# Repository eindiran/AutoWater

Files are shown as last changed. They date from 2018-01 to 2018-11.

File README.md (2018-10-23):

# AutoWater
AutoWater is a project which automates watering a potted plant by measure soil moisture levels using a capciative moisture sensor. If the water levels are beneath a threshold, AutoWater will trigger a normally-closed solenoid valve, pumping water into the pot.

## Ingredients
In order to begin this project you will need:
- __Arduino Uno__ or compatible board, with a __9v power supply__ (1)
- __TIP 120 transistor__ (1)
- __1N4007 Diode__ (1)
- __1k Ohm Resistor__ (1)
- [__Analog Capacitive Soil Moisture Sensor v1.0__](https://www.dfrobot.com/wiki/index.php/Capacitive_Soil_Moisture_Sensor_SKU:SEN0193) (1)
- __Breadboard__ (1)
- __Jumper wires__ (10+)
- __Alligator clamps__ (2)
- __Solenoid Valve__ (1)
- __Plastic tubing__ (10 feet)
- __Potted plant__ (1)

## Reading the moisture sensor
The first step is to set up the moisture sensor and get a reading off of it.
In the tests directory, there is a file which can be used to run the test: `MoistureSensorTest.ino`

Place the moisture sensor carefully in the potted plant, leaving the wire section exposed. Notice that on the sensor there is a horizontal white line: *do not submerge the sensor beyond this line*, as it is possible to damage the sensor if the top gets wet. Ideally place the sensor such that the dirt level is approximately __1 inch__ below this.

Take three jumper wires (1 red, 1 black, 1 blue). Match them to the same colors coming off of the sensor. Run the red wire into the __5v__ pin on the Arduino: this will provide power to the sensor. Next run the blue wire to the __Analog 0__ pin, and the black wire to the ground pin (__GND__).

### Moisture Sensor diagram
Here is a diagram showing the connections between the Arduino and the moisture sensor:

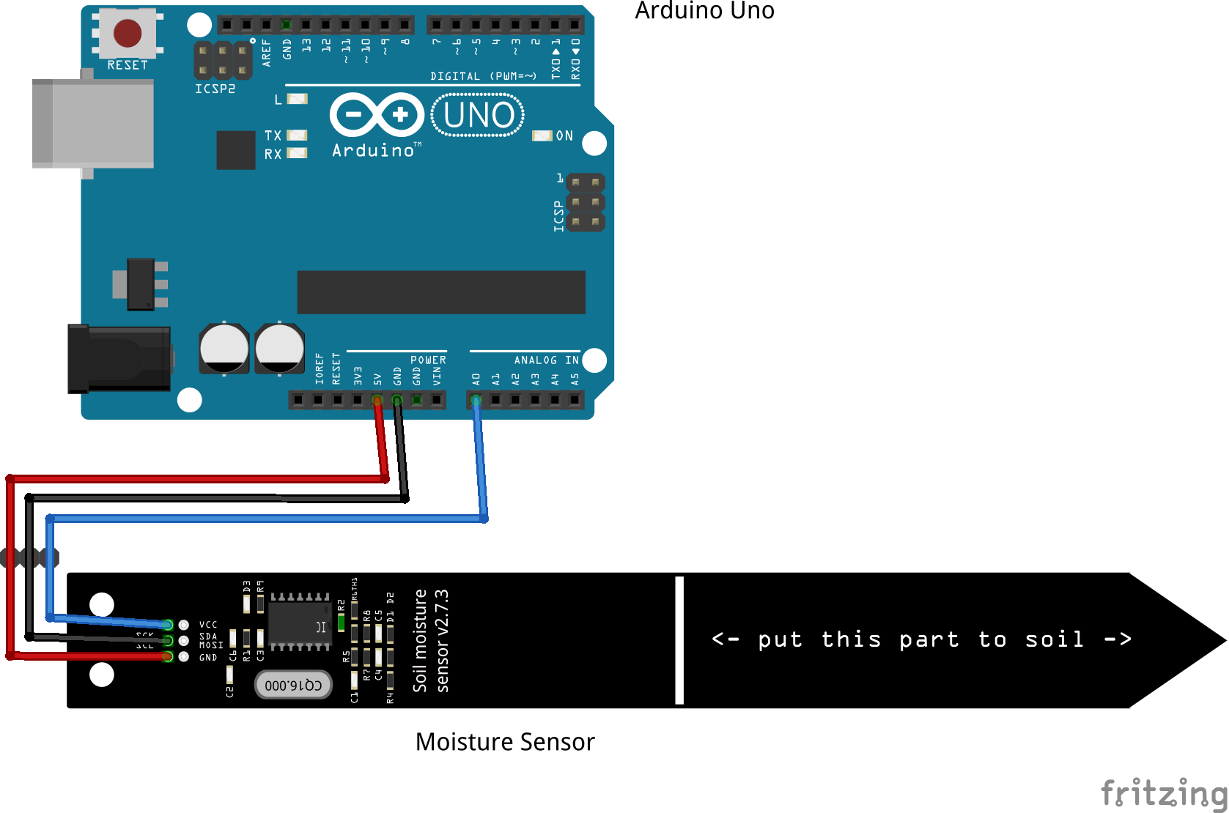
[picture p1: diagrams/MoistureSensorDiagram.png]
Moisture Sensor Diagram


### Testing the moisture sensor
Plug in the Arduino to your computer, then open the __Arduino IDE__ and upload `MoistureSensorTest.ino` to it. If you get permissions issues and can't upload it, look up the error message it spits out. Likely you will need to run a command like `sudo chmod a+rw /dev/ttyACM0`, which will give you write permissions for the Arduino.

Once you have successfully uploaded the file to the board, from the __Tools__ menu of the IDE, select __Serial Monitor__. If everything has been set up correctly, the window which opens will display a reading from the sensor which is updated every few seconds.
If the monitor displays nonsensical symbols instead of human-readable text, make sure that the baud rate for the monitor matches what is set in the code: using the vanilla code, set to __9600 Bd__.

In order to be sure that the sensor is working proper, after you have begun to see readings from it, slowly add water to the plant. Pour carefully, taking care to not splash the sensor directly. Gradually the reading from the sensor should *decrease* in value.

### Calibrate moisture sensor (optional)
This step is optional, depending on the accuracy you want the moisture sensor to report human-readable moistures with (e.g. "75% Humidity").

To calibrate your moisture sensor, follow the steps above to set it up for testing. In addition you will need a glass of water. First, dry off the moisture sensor entirely. Then fire up `MoistureSensorTest.ino`, and record the value that the sensor reports while held outside of any soil, in the air. Write down this value, which will be used as the 0% Humidity value.

Next, submerge the sensor up to the horizontal line in the glass of water. After the readings stabilize, write down the number, as this will be used as the 100% Humidity value.

Once we've captured these two values, open up the Arduino IDE, as we are going to make some small changes to the code. First find a global variable named `DEBUG`. It is set to __0__. Change the value to __1__. Next, find the variables `AIR_VALUE` and `WATER_VALUE`.
Change the value for the first from __1000__ to the number you recorded when calibrating the moisture sensor in the air.
Next, change the value for the second from __200__ to the value you recorded when calibrating the moisture sensor in the cup of water.
Finally, we need to make the interval correct. Find the variable `INTERVAL`. You need to set this value to `(AIR_VALUE - WATER_VALUE)/4`. Originally the variable was set like so: (1000 - 200)/4 = 800/4 = 200. If the result gives you a fraction, round to the nearest integer.

Save the code and re-upload it to the Arduino. Re-run the test in the air, water and soil, and see what values you get. Now you should see lines like "*Humidity: >50%*" in the output, which indicates that the humidity is >50 % and <75 % of `WATER_VALUE`.

## Turning the Solenoid Valve
Here is a diagram showing the setup of the solenoid valve.
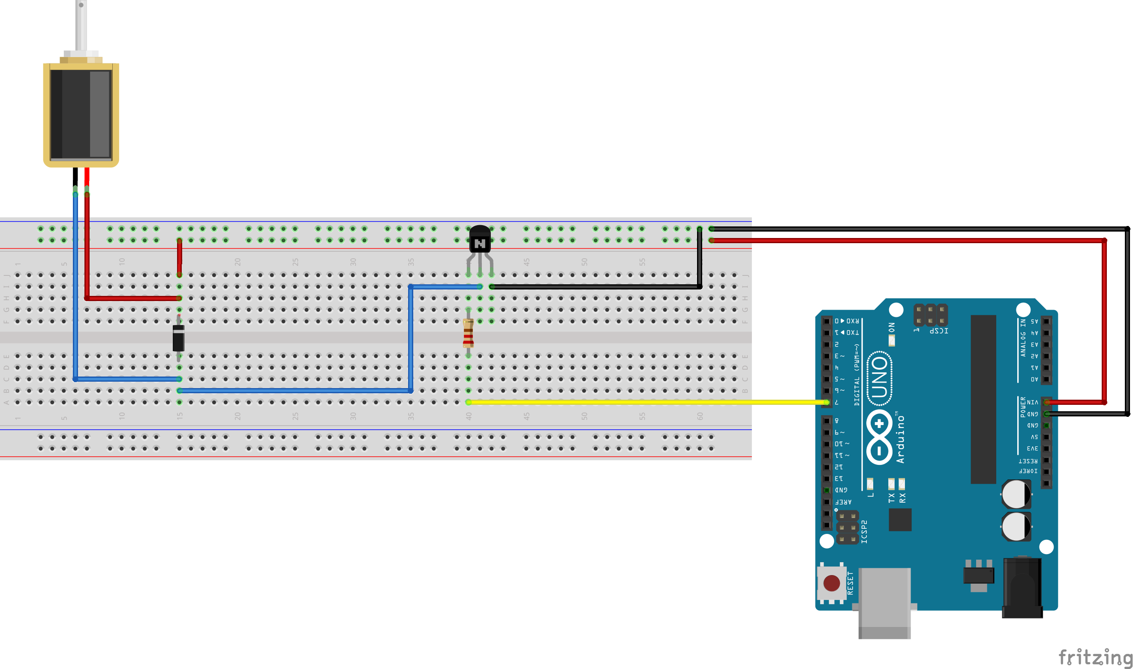
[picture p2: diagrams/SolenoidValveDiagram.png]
Solenoid Valve setup


The setup in this section is based on a tutorial from BC Robotics, which can be found [here](https://www.bc-robotics.com/tutorials/controlling-a-solenoid-valve-with-arduino/).

Note that none of the pins used here overlap with those used during the moisture sensor test. As a result, you don't need to unplug anything from the previous step. If you leave the moisture sensor plugged in during the next step, all the pieces will be correctly set up.
If you want to just play around with the solenoid valve setup, however, feel free to start with a clean breadboard.

### Setting up the power to the solenoid valve
To begin with turn the breadboard so that __j1__ is in the top left corner. Next, take a red wire and connect it to the __Vin__ pin on the Arduino. Plug this in to the __positive rail__ on the top right of the breadboard. This will take the direct voltage from the __9v__ power supply and pass it to the solenoid valve, without first sending it to the board's regulator. If you tried to use a lower voltage, the solenoid valve would not be able to turn. With another red wire connect the positive rail to the near end of a column, on the left side of the breadboard. Immediately below plug in another red wire; take an __alligator clamp__ and attach it to this wire. Connect the other end of this alligator clamp to the __positive__ side of the __solenoid valve__.

### Setting up the Diode
Take the __diode__ and put the side with the __white line__ immediately beneath the last wire plugged in to the breadboard. Plug the other end into __row c__ of the same column. In __row b__ plug in a black wire. Take the second alligator clamp and attach it first to this black wire, then to the __negative__ side of the solenoid valve.

### Setting up the Transistor
Take the __TIP-120 transistor__ and find the front. With the transistor facing you, plug all three pins into three columns in __row j__ beginning several columns to the right of the diode column. Take a black wire and plug it first into __row a__ of the diode column, then into __row i__ of the column containing the transistor's __middle pin__. Take the __resistor__ and plug it into the column of the __left pin__, leaving at least one open pin; in __row a__ of the same column, plug in a yellow wire. Plug the other end of the yellow wire into __digital pin 7__ on the Arduino.

### Setting up the ground
In the column of the __right pin__ of the transistor, add a black wire. Run this wire into the __ground rail__ at the top of the breadboard. Take another black wire and run it from one of two __GND__ pins on the Arduino to the ground rail on the breadboard. The circuit is now complete!

### Running the tests
Open up the IDE and connect the Arduino to your computer. Upload the file `SolenoidTest.ino`. Pick up the solenoid valve and put it next to your ear. You should hear it turn once per second.

Unplug the Arduino. Take a short length of __aquarium tubing__ and cut it off, placing one end inside the solenoid valve and the other end inside the __water reservoir__ or __pump__. Cut off a second length of tubing and put it into the other side of the solenoid valve. For the test, place this other end inside a bucket.

Plug the Arduino back in and run `SolenoidTest.ino` again. The valve should alternate between opening for a second and closing for a second, letting water out into the bucket each time it is open.

## Putting it all together
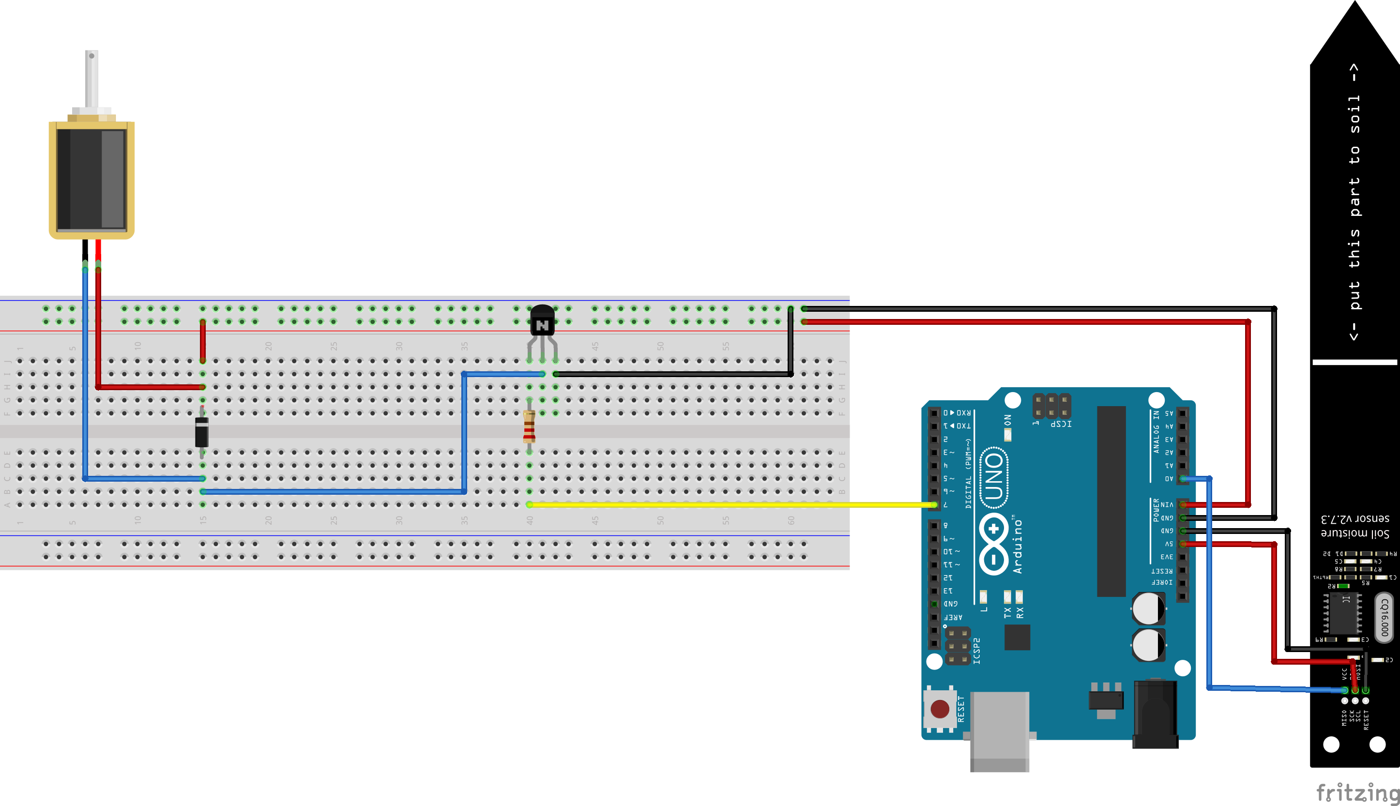
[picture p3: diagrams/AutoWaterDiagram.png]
AutoWater diagram

If you didn't unplug the moisture sensor during the last step, congratulations! You are almost ready to run AutoWater. If you did, follow the instructions for plugging in the moisture sensor while leaving all the wires from setting up the solenoid valve plugged in.

The last step before you run everything is connecting the potted plant. First place the moisture sensor in the soil, then take the output side of the tubing amd place it so that the output water will end up watering the plant, but not directly on the moisture sensor.

Open up `AutoWater.ino` in the IDE and edit the file to fit the values calibrated during the moisture sensor testing phase. Set the `DEBUG` value to the appropriate level of logging: __0__ has minimal logging, __1__ has normal logging, and __2__ has logging set to max while disabling the actual watering functionality. This last mode is very useful for debugging and experimenting.

Upload the completed file to the Arduino and open the __Serial Monitor__. Immediately you should see a reading from the moisture sensor. If that reading is too low and `DEBUG < 2`, AutoWater will water your plant! Once you've played around for a bit and have a good idea of how things work, change the time variables to fit the watering needs of your plant. Now you can happily go about your day knowing that the needs of your plant are being taken care of!

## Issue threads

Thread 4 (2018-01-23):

Fix Moisture Sensor Diagram

eindiran, 2018-01-23:
Fix Moisture Sensor Diagram to have red wire point into 5v on Arduino Uno.

eindiran, 2018-01-28:
Fixed a while back but forgot to close the issue.

Closed 2018-01-28.

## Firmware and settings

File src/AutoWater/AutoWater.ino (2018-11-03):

/**
 * AutoWater.ino
 * Automate watering a plant using a solenoid valve
 * and a moisture sensor.
 * Author: eindiran <eindiran@uchicago.edu>
 */

/** Initialize globals */
const int DELAY_SECONDS = 5;   // Time between moisture checks
const int AIR_VALUE = 1000;    // Replace this value with sensor reading of air
const int WATER_VALUE = 200;   // Replace this value with sensor reading of water
const int INTERVAL = 200;      // Replace this with (AIR_VALUE - WATER_VALUE)/4
const int DRY_THRESH = 425;    // The moisture value beneath which you water
const int SOLENOID_PIN = 7;    // Arduino pin tied to the SV
const int WATER_TIME_MS = 450; // Time to open the SV in ms
const int DEBUG = 1;           // 0,1,2 toggle verboseness off-low-high
                               // 3 and > turn off watering, but preserve verboseness

/**
 * setup() --> One-time setup tasks go here.
 * Opening up the serial port, set the baud rate to 9600 and prep the SV's pin.
 */
void setup() {
  Serial.begin(9600);
  pinMode(SOLENOID_PIN, OUTPUT);
}

/**
 * get_moisture_level() --> Sets a string encoding moisture level.
 * Uses ranges / buckets to define moisture level. These buckets
 * allow you to determine to a coarse degree how moist it is.
 */
void get_moisture_level(int moisture_val, String &moisture_level) {
  switch (moisture_val) {
    // This special form of `case` syntax is supported by gcc and therefore by Arduino
    // It allows you to specify a range; `case A ... B` is true whenever the value being
    // switched on is between A and B.
    case (WATER_VALUE - 100) ... WATER_VALUE:
      moisture_level = "Humidity: 100%";
      break;
    case (WATER_VALUE + 1) ... (WATER_VALUE + INTERVAL):
      moisture_level = "Humidity: >75%";
      break;
    case (WATER_VALUE + INTERVAL + 1) ... (WATER_VALUE + 2 * INTERVAL):
      moisture_level = "Humidity: >50%";
      break;
    case (WATER_VALUE + 2 * INTERVAL + 1) ... (WATER_VALUE + 3 * INTERVAL):
      moisture_level = "Humidity: >25%";
      break;
    case (WATER_VALUE + 3 * INTERVAL + 1) ... AIR_VALUE:
      moisture_level = "Humidity: >0%";
      break;
    default: // Humididty level of soil is less than humidity in air
      moisture_level = "Humidity: 0%";
      break;
  }
}

/**
 * moisture_percentage() --> Returns an int representing the humidity
 * percentage. It is calculated based on the range of the baseline values
 * for AIR_VALUE and WATER_VALUE.
 */
int moisture_percentage(int moisture_val) {
  int moisture_range = AIR_VALUE - WATER_VALUE;
  return ((moisture_val - WATER_VALUE) * 100) / moisture_range;
}

/**
 * get_moisture_percentage() -->  sets a string encoding the moisture level 
 * as an exact percentage. The sensor may drift, so this percentage can appear to
 * "float" around.
 */
void get_moisture_percentage(int moisture_val, String &moisture_level) {
  int moisture_pcent_val = moisture_percentage(moisture_val);
  moisture_level = "Humididty: " + String(moisture_pcent_val) + "%";
}

/**
 * nc_turn_solenoid() --> Puts a normally-closed solenoid valve
 * into its open state for num_seconds, then closes it.
 */
void nc_turn_solenoid(int num_seconds) {
  int num_ms = num_seconds * 1000;
  if (DEBUG) {
    Serial.print("Opening solenoid valve for "); Serial.println(num_seconds);
  }
  digitalWrite(SOLENOID_PIN, HIGH); // Switched magnet on; open
  delay(num_ms);
  digitalWrite(SOLENOID_PIN, LOW);  // Switched magnet off; closed
  if (DEBUG) {
    Serial.println("Solenoid valve closed.");
  }
}

/**
 * water_plant() --> Water the plant based on the moisture sensor readings.
 */
void water_plant(int moisture_val) {
  if (moisture_val > DRY_THRESH) {
    if (DEBUG) {
      Serial.println("Moisture beneath threshold: watering plant.");
    }
    nc_turn_solenoid(WATER_TIME_MS);
  } else if (DEBUG) {
    Serial.println("Moisture level above threshold: not watering plant.");
  }
}

/**
 * print_sensor_value() --> Print the exact sensor value. Takes a single
 * int as input.
 */
void print_sensor_value(int val) {
  Serial.print("Moisture Sensor Value:\t"); Serial.println(val);
}

/**
 * loop() --> Main loop of the program.
 * (1) Read moisture sensor.
 * (2) Print out information about the sensor if necessary.
 * (3) If the moisture level is beneath the dryness threshold,
 *     we now try watering the plant via water_plant().
 * (3) Wait a reasonable period of time before checking the sensor
 *     again.
 */
void loop() {
  int moisture_val;             // reading from moisture sensor
  moisture_val = analogRead(0); // connect sensor to Analog 0
  print_sensor_value(moisture_val);
  if (DEBUG == 1) {
    // Print human-readable moisture levels, as buckets
    String moisture_level;
    get_moisture_level(moisture_val, moisture_level);
    Serial.println(moisture_level);
  } else if (DEBUG > 1) {
    // Print human-readable moisture levels, as percentages
    String moisture_level;
    get_moisture_percentage(moisture_val, moisture_level);
    Serial.println(moisture_level);
  } else if (DEBUG > 2) {
    // Check sensor, without actually activating the SV
    delay(DELAY_SECONDS * 1000);
    return;
  }
  // If your DEBUG was > 2, you expect to skip this step.
  water_plant(moisture_val);
  delay(DELAY_SECONDS * 1000);
}

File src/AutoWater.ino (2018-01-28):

/**
 * AutoWater.ino
 * Automate watering a plant using a solenoid valve
 * and a moisture sensor.
 * Author: eindiran <eindiran@uchicago.edu>
 */

// Initialize globals.
int DEBUG = 0;
int DELAY_SECONDS = 15; // time between moisture checks
int AIR_VALUE = 1000; // Replace this value with sensor reading of air
int WATER_VALUE = 200; // Replace this value with sensor reading of water
int INTERVAL = 200; // Replace this with (AIR_VALUE - WATER_VALUE)/4
int DRYNESS_THRESHOLD = 425;
int SOLENOID_PIN = 4;
int WATER_TIME = 4; // time to open SV in seconds

/**
 * One-time setup.
 */
void setup() {
  Serial.begin(9600); // set the baud rate
  pinMode(SOLENOID_PIN, OUTPUT); // Prep the SV's pin.
}

/**
 * Sets a string encoding moisture level.
 * This function was inspired by the test code here:
 * https://www.dfrobot.com/wiki/index.php/Capacitive_Soil_Moisture_Sensor_SKU:SEN0193
 */
void get_moisture_level(int moisture_val, String &moisture_level) {
  if (moisture_val <= WATER_VALUE) {
    moisture_level = "Humidity: 100%";
  } else if (moisture_val <= (WATER_VALUE + INTERVAL)) {
    moisture_level = "Humidity: >75%";
  } else if (moisture_val <= (WATER_VALUE + 2*INTERVAL)) {
    moisture_level = "Humidity: >50%";
  } else if (moisture_val <= (WATER_VALUE + 3*INTERVAL)) {
    moisture_level = "Humidity: >25%";
  } else if (moisture_val <= (AIR_VALUE)) {
    moisture_level = "Humidity: >0%";
  } else {
    moisture_level = "Humidity: 0%";
  }
}

/**
 * Puts a normally-closed solenoid valve into its open
 * state for num_seconds, then closes it.
 */
void nc_turn_solenoid(int num_seconds) {
  int num_ms = num_seconds * 1000;
  if (DEBUG) {
    // Poor-man's printf
    Serial.print("Opening solenoid valve for "); Serial.println(num_seconds);
  }
  digitalWrite(SOLENOID_PIN, HIGH); // Switched magnet on; open
  delay(num_ms);
  digitalWrite(SOLENOID_PIN, LOW); // Switched magnet off; closed
  if (DEBUG) {
    Serial.println("Solenoid valve closed.");
  }
}

/**
 * Water our plant based on the moisture sensor reading.
 */
void water_plant(int moisture_val) {
  if (moisture_val > DRYNESS_THRESHOLD) {
    if (DEBUG) {
      Serial.println("Moisture beneath threshold: watering plant.");
    }
    nc_turn_solenoid(WATER_TIME);
  } else if (DEBUG) {
    Serial.println("Moisture level above threshold: not watering plant.");
  }
}

/**
 * Print sensor value.
 */
void print_sensor_value(int val) {
  Serial.print("Moisture Sensor Value:\t"); Serial.println(val);
}

/**
 * Main loop.
 */
void loop() {
  int moisture_val; // reading from moisture sensor
  moisture_val = analogRead(0); // connect sensor to Analog 0
  if (DEBUG) {
    print_sensor_value(moisture_val);
    if (DEBUG > 1) {
      // if DEBUG > 1 print human-readable moisture level
      String moisture_level;
      get_moisture_level(moisture_val, moisture_level);
      Serial.println(moisture_level);
    }
    if (DEBUG > 2) {
      // if DEBUG > 2, check sensor w/o watering
      delay(DELAY_SECONDS * 1000);
      return;
    }
  }
  water_plant(moisture_val);
  delay(DELAY_SECONDS * 1000);
}

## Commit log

2018-01-21 Initial arduino code for testing sv and moisture sensor.
2018-01-21 Adding section of setting up moisture sensor
2018-01-22 Adding test for calibrating the initial moisture sensor setup.
2018-01-22 Cleaning up SolenoidTest
2018-01-22 Adding diagram for moisture sensor
2018-01-28 Fix wire going from 3.3v pin to correct 5v pin
2018-01-28 Improve Readme with ms calibration info
2018-01-28 Adding human readable moisture output to AutoWater. Fixing comment.
    [AutoWater.ino, MoistureSensorTest.ino]
2018-01-28 Moving files to please Arduino IDE
2018-01-28 Adding Fritz src files and new diagram
    [MoistureSensorDiagram.fzz, SolenoidValveDiagram.fzz]
2018-01-28 Change solenoid pin to D7
2018-01-28 Update SOLENOID_PIN to digital 7
2018-01-28 Adding info on SolenoidTest
2018-01-28 New diagram
    [AutoWaterDiagram.fzz]
2018-10-15 Switch instead of giant if block
